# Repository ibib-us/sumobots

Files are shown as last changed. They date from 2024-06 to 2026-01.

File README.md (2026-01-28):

# IBiB Sumobots

It Begins in Brockport (IBiB) is developing its own sumobot league to introduce the community to competitive robotics.

Sumobots are robots that compete to push one another out of a ring. Ours are autonomous, which means they need to figure out how to do this all on their own. Ours are also built using inexpensive and easy-to-acuire materials, which means you can try out autonomous competitive robotics without having to invest a lot of cash.

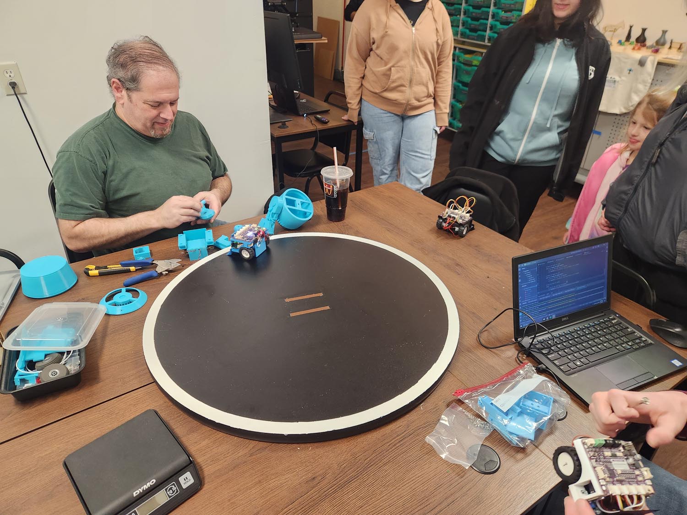
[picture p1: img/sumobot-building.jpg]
Sumo Louis


Here, you will find the hardware, the software and the rules for sumobots.

# Hardware

To be written. The files you need to 3D print the body of your sumobot are in the [stl](/stl/) directory.

# Software

The software can be found in the [code](/code/) directory. There are four files that are needed for your sumobot to run:

- `base_bot.py` contains the startup, searching, turning, and charging routines, along with some utility functions
- `code.py` is the main program that includes the fight sequence and the routine to start fighting
- `settings.py` contains parameters you can change to customize the fighting style of your sumobot
- `adafruit_vl5310x.mpy` is a special library to allow the time of flight (distance) sensor to operate properly

# Downloading the correct driver for the distance sensor

The sensor library you download depends on the version of CircuitPython you are running. The version can be found by looking at the `boot_out.txt` file on your sumobot. It will look something like this:

>Adafruit CircuitPython 7.1.0 on 2021-12-28; Cytron Maker Pi RP2040 with rp2040
>Board ID:cytron_maker_pi_rp2040

Since this sumobot is running version 7, it requires the version 7 library. However, Adafruit no longer supports this version, and it is recommended we upgrade to the latest (which is 9 at the moment - this is the version you can find in this repository). Here are the steps:

- Head to CircuitPython.org and download the `.UF2` file for the microcontroller. The direct link is [here](https://circuitpython.org/board/cytron_maker_pi_rp2040/).
- Find the `RST` button on your MakerPi2040 and double click it. You will now see that the CIRCUITPY drive on your computer disappears and is replaced by RPI-RP2.
- Copy the `.UF2` file that you downloaded onto this drive. Once completed, the RPI-RP2 drive will disappear
- Head over to the [Libraries](https://circuitpython.org/libraries) section and download the appropriate bundle, which is currently version 9.

## Initial setup
Open `settings.py` and review the "Robot hardware settings" section. Change any pin values if your hardware is connected differently than the default settings.

## Installation instructions
Make a backup copy of the code.py file that cam on your MakerPi board.
Copy the files `base-bot.py`, `code.py`, `adafruit_vl53l0x.mpy`, and `settings.py` to your MakerPi to get a working sumo bot.

## How to use
Turn on your MakerPi. To start a bout hold down the GP20 button until the light turns yellow. Your bot is now armed. Release the button to start the bout after a 5 second delay.
See the rules document for more detail on how Sumo bot matches operate.
Turn on your Maker Pi and press buttons until you find the one that turns the lights from red to yellow. Your bot is now armed. Release the button to enter FIGHT MODE!

## How to customize
Change values in the "Settings that control fight mode parameters" section of `settings.py` to make adjustments to your robot's fighting strategy.

## Advanced customization
Modify the `fight()` method in code.py to change your robot's fighting strategy.

## File descriptions 
* `settings.py` contains hardware pin assignments and basic behavior settings
* `code.py` defines the `fight()` method which determines the robot's logic while in fight mode.
* `base_bot.py` contains the main class which defines the fundamental methods for robot control such as moving and detecting enemies.
* `adafruit_Vl530x.mpy` is the driver for the time of flight sensors. The robot code won't work without it installed on the MakerPi.
* `original_code.py` is the default demo program that shipped with the MakerPI RP2040. It's not needed for the robot to work.

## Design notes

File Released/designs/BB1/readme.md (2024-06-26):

This is the complete plans for a mini sumo robot that conforms to IBiB2040 rules and is based around the Maker Pi RP2040 robotics board. It also comples with the generally used mini sumo rules.

An illustrated complete parts list is included in the "parts preparation.pdf" document.

Stl files for 3D printing the four body parts are included.

Illustrated assembly instructions can be found in the "assembly instructions.pdf" file.

Some notes on testing and changing the robot can be found in the "testing and tweaking.pdf" file.

The Maker Pi board should be running CircuitPython (it ships this way) and will need the code files in the code folder copied to it.

All material in this archive except the adafruit_vl53l0x.py file is CC0 "no rights reserved." adafruit_vl53l0x.py has a MIT license.  
Send any questions to: bill@tinkerfam.net

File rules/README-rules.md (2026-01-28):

# Rules README

*Note:* These rules are based on the gen 1 design (10 cm x 10 cm). They will be updated shortly.

- [rules for building your bot](./rules-robot.md)
- [rules for competing in a sumobot match](./rules-arena.md)

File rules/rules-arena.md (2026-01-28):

# IBiB Sumobot Arena Rules

**Event Summary:** Two robots compete in a head-to-head match following the basic system of traditional human sumo wrestling. Robots are autonomous. The objective is for a robot to push its opponent outside of the arena (doyho).

## I. Event Structure

### A. Arena

1. Competition area
    1. The name of the competition area is *dohyo*.
    2. The ring shall be circular in shape and 76 cm-77 cm (30 inches) in diameter. 
    3. The surface will be painted black or be blackbplastic with a 1 cm white line for a border. 
    4. The ring area extends to the outside edge of this circular line. 
    5. The dohyo will be at least 2.5cm in thickness.
2. Shikiri lines (starting lines) 
    1. Two painted parallel brown (or equivalent for absorption of IR light) lines centered in the ring
    2. The dimension of the shikiri lines are 1 cm in width, 10cm in length.
    3. The shikiri lines are spaced 10cm apart. 
    4. The separation distance between the lines is measured to their outside edges.
3. Dohyo exterior
    1. The area surrounding the dohyo is the *Shuhen*.
    2. There should be an appropriate space for recovering robots outside the outer edge of the ring. 
        1. This space can be of any color, and can be of any material or shape as long as the basic concepts of these rules are not violated. 
    2. This area, with the ring in the middle, is to be called the *arena*. 

**comments** The exact material for the dohyo is not specified. It may not be necessary to specify a material, only a set of characteristics such that the edge detection sensors can be adjusted to trigger only on the border and not on the shikiri lines and that the surface is suitable for the standard 2040b class blade and wheels. Should we add a diagram of the dohyo? Should we have a minimum distance for the shuhen?

### B. Format

1. The event is a double-elimination tournament. 
    1. Seeding is done randomly based upon the number of contestants entering the competition. 
    2. In the event that the bracket incorporates byes, they will be filled randomly.
2. Each robot competes in matches consisting of up to three bouts.
3. The winner of a match is the robot that wins two out of three bouts.
4. The winner of each match moves on in the winners bracket.
5. The loser of each match, if it is their first loss, moves to the losers bracket.
6. Ties are addressed in the section `C. Bout`
7. A robot is eliminated from the event after its second loss.
8. The judge overseeing the event is the gyoji.

### C. Bout 

1. A bout lasts a maximum of three minutes.
2. Contestant Positioning
    1. Contestants stand by the dohyo behind their respective shikiri lines.
3. Robot placement
    1. At the gyoji's command of "Position bots," contestants must immediately hold their robots directly over the area they intend to place them, approximately 15cm (6 inches) above the dohyo.
    2. The gyoji will then give the command "Place Bots," at which point contestants must lower their robots straight down onto the dohyo in one continuous motion, ensuring the final orientation is set during this movement.
    3. No additional adjustments to the robot's position or orientation are allowed after it has been placed on the dohyo.
    4. Failing to comply with these placement rules may be considered a minor violation. 
4. Starting the bout
    1. The robots must conform to the startup sequence described in `II.A. startup sequence`
    1. The gyoji instructs the contestants to arm their robots.
    2. With a countdown ("three, two, one, release"), the contestants initiate the start sequence of their robots and step away from the dohyo.
        1. Contestants should step away at least 30 inches from the edge of the dohyo.
5. False Start
    1. The gyoji may declare a false start if a robot starts before the word "release".
    2. The gyoji will declare a false start if they hear an audible sound from one of the robots prior to saying the word "release".
    3. After a false start, the offending robot is issued a penalty (shido).
    4. A robot receiving two shidos loses the bout.
6. Scoring and stopping the bout
    1. Earning points (Yuhkoh):
        1. A Yuhkoh is earned when a robot successfully pushes its competitor outside of the dohyo.
        2. A Yuhkoh is also earned if the competitor's robot exits the dohyo on its own.
        3. A Yuhkoh is awarded to a robot if its competitor receives two shidos.
    2. The Gyoji may stop a bout under several conditions
        1. A player is injured or about to be injured.
        2. The robots display no forward progress in the bout for 10 seconds.
        3. A robot is about to damage the dohyo.
        4. A robot has violated one of the rules.        
    3. Should a bout end with no contestant leaving the dohyo, gyoji will decide a winner and award a yuhkoh based upon technical merits in movement and operation of the robot, penalties accrued during the bout, and contestant attitudes during the bout.

**Comments** Should we provide examples of the decision making process in the event of a tie? It is possible that the gyoji cannot differentiate between the two sounds the robots are making, and therefore makes it difficult to determine who commits a false start. 

## II. Additional robot regulations

### A. Startup sequence
1. A startup sequence must be initiated by the press of button GP20
    1. Pressing and holding the GP20 button is referred to as "arming the robot".
    2. Releasing the GP20 button will continue the startup sequence.
2. The startup sequence must emit an audible tone to indicate the sequence has started
3. The startup sequence must blink the neopixel LEDs at 1 second intervals
4. The startup sequence must last for at least 5 seconds.
5. The wheel motors must be off during the startup sequence.

### B. Robot upgrades during competition
1. Contestants are not allowed to modify their robots after completing the class verification procedure unless specificly mentioned in these rules.
2. Sensor calibration (e.g. adjusting the potentiometers of edge detectors) 
    1. Utilizing the dohyo for sensor calibration is allowed prior to the start of the competition. 
    2. Contestants my not calibrate any sensors during their match.
    3. Contestants may perform sensor calibration without the use of the dohyo at other times during the competition.
3. Power (e.g. checking and replacing batteries)
    1. Batteries cannot be replaced after robots have completed their calss verification procedure.
    2. Under special circumstances, gyoji or the event manager may permit battery replacements, which will require class reverification. 

**Comments** Should we indicate the frequency and duration of the startup tone? Are there other startup sequence standardizations that should be implemented? Note that the mass difference between the super cheap zinc oxide and standard alkaline batteries is significant, so battery swap outs could result in a verified bot exceeding the weight limit.

## III. Violations and penalties

### A. Violations

1. Major violations
    1. A player who utters insulting words or puts voice devices in a robot to utter insulting words, or writes insulting words on teh body of a robot, is in violation of these rules.
2. Minor violations
    1. Entering the arena during the round without legitimate reason.
    2. Demanding to stop a match without appropriate reason.
    3. Taking more than 30 seconds before resuming a bout unless gyoji has announced a time extension.

### B. Penalties

1. In the event of a major violation, the contestant receives a kinjite (disqualification). All robots entered under the contestant are removed from the event.
2. In the event of minor violoation, the offending robot recieves a shido. Two shidos within one bout results in a Yuhkoh for the opponent.

## IV. Miscellaneous

### A. Declaring objections
1. No objections shall be declared against gyoji's decisions

### B. Safety Protocols
1. *reserved*

### C. Code of Conduct
1. *reserved*

### D. Technical Support
1. *reserved*

## V. Definitions

Bout
: A single 3-minute competition between two robots

Event
: A series of matches organized into a double-elimination bracket

Gyoji
: The referee/judge of a match.

Kinjite
: Disqualification from an event due to a major violation of the rules.

Match
: A series of up to three bouts

Shido
: A minor penalty. Two shidos within a bout results in a Yuhkoh for the opponent.

Yuhkoh
: A point, indicating that a bout has been won.

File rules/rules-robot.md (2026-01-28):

# IBiB Sumobot Design Rules

## I. General Specification

### A. Robot Classes

1. 2040b
    1. Must fit within a 10 cm by 10 cm square tube, with no height restriction.
    2. Maximum weight: 500 grams.
    3. Powered by no more than 6 volts.
    4. Must use the Maker Pi RP2040 development board as the microcontroller.
    5. Only the VL53L0X time of flight sensor and TCRT5000 reflectance sensor are allowed.
    6. Only two N20 metal gear DC motors are allowed.
    7. Must be programmed using CircuitPython.
2. 2040b+
    1. The 2040b+ class follows all the rules of the 2040b class except where specifically noted.
    2. No restrictions on the type and number of sensors.
    3. No restriction on the type and number of motors.

## B. Autonomy

1. All robots must be autonomous.
2. Any method of onboard control may be used, as long as it is fully contained within the robot and receives no external signals or directions (human, machine, or otherwise).
3. Autonomous robot operation must begin within the start procedure indicated for the event and robot class.

## C. Identification

1. Robots must have a name or number for registration purposes.
2. Robots must be clearly identifyable by their name and/or number.

## II. Restrictions

### A. Prohibited Devices and Materials

1. Jamming devices, such as IR LEDs intended to saturate the opponent's IR sensors, are not allowed.
2. Parts that could break or damage the event area are not allowed.
3. Parts intended to damage the opponent’s robot or its operator are not allowed. 
4. Parts intended to damage or alter the event area are not allowed.
5. Devices that can store liquid, powder, gas, or other substances for throwing at the opponent are not allowed.
6. Flaming devices are not allowed.
7. Devices that throw things are not allowed.
8. Sticky substances to improve traction are not allowed.
    1. Tires and other components of the robot in contact with the event area must not be able to pick up and hold a standard 3"x5" index card for more than two seconds.
    2. Devices to increase downforce, such as a vacuum pump or magnets, are not allowed.
9. All edges, including but not limited to the front scoop, must not be sharp enough to scratch or damage the ring, other robots, or players. Edges with a radius greater than 0.005", as would be obtained with an unsharpened 0.010" thick metal strip, should be acceptable. Judges or competition officials may require edges deemed too sharp to be covered with tape.

### B. Exceptions to restrictions

1. Restrictions mentioned in this section may be superceded by the event rules.
2. The judge or referee overseeing an event has final say on the interpretation of these restrictions.

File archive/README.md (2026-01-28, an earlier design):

# Archive

The archive contains older builds and design ideas for sumobots. They remain for historical value but we do not recommend they be used in current sumobot designs.

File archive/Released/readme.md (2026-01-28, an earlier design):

These files are released for public use as a starting point for builds of the IBIB2040 class of Mini Sumo Bots.
A rules document for competition is included.  
An example build is provided in the designs/BB1 folder. This includes a parts list and preparation document, an assembly document, and 3D printable files to create a chassis. A limited number of kits from this build are available.  
Software to be downloaded to the Maker PI2040 board can be found in the code folder.  
General information about the project can be found at https://ibib.us/projects/mini-sumo-robots/  
Send all inquries to Bill at bill@tinkerfarm.net.  

two

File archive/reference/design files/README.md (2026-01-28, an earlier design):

# sumobots
Schematics and datasheets for building and programming IBiB mini sumo bots
Contact Bill Ball, bill@tinkerfarm.net with any questions.

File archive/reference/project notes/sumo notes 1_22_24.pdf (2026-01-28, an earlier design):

IBiB Mini Sumo project notes. 1/21/2024. Bill Ball

The bots will meet standard specifications: 10cm x 10cm x unlimited, 500 grams max.

The bots will have the following components:

1. 4xaa battery holder. $0.5-$1. Is the 1x4 or 2x2 layout better? Builders supply their own batteries.

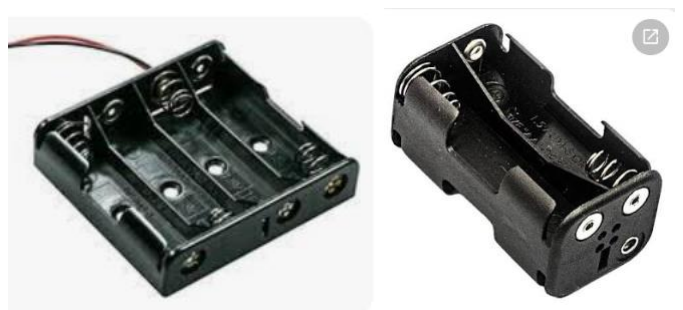
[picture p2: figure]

2. Maker Pi RP2040 main board with OEM Circuitpython 7 and accompanying 4 x grove to header pin wire sets. Cheapest source in bulk @$10: Newark. Manufacturer reference: https://www.cytron.io/p-maker-pi-rp2040-simplifying-robotics-with-raspberry-pi-rp2040 (https://www.cytron.io/p-maker-pi-rp2040-simplifying-robotics-with-raspberry-pi-rp2040)

The adafruit_vl5310x.mpy library will be installed by us. The default code.py will be renamed and a basic sumo bot program will be added as code.py.

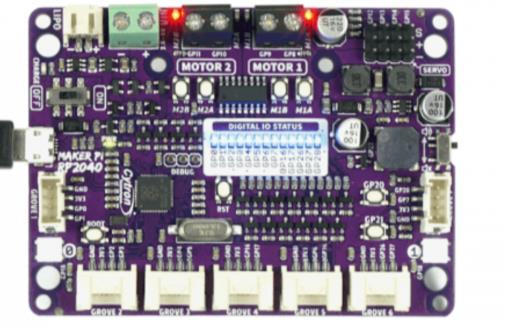
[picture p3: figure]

3. N20 6V motors (2). What rpm/torque trade off is best? We will start at 150rpm. $4.20 per pair from Aliexpress. We will need to solder on leads. Mounting brackets will be 3D printed (standard ones are too short for the wheels).

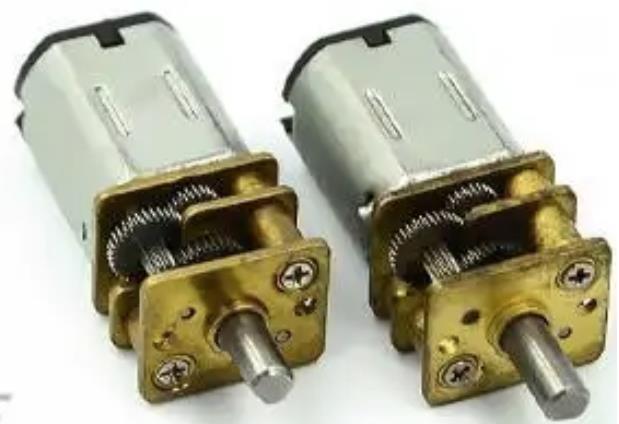
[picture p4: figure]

### 4. K346 43*19*3mm D-hole Rubber Wheel (2). $1.5 per pair from Aliexpress

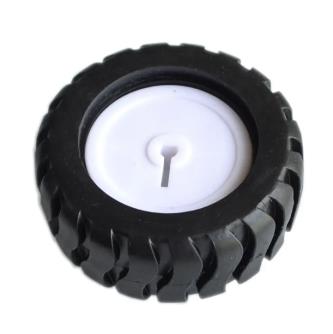
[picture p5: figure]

5. VL53L0X Time-of-Flight Ranging Sensor (2). $2.60 per pair from Aliexpress. We will need solder the header pins. We will use the VCC, GND, SCL, SDA, and XSHUT pins. XSHUT is required to change the I2C address in software. We are not planning to use the GPI01 (data ready) pin (it would require an additional grove wire set if we do). If two sensors doesn’t work well we may need to go to three, which would require 2 additional grove wire sets and may not all fit on the same I2C bus as exposed by the Maker pi.

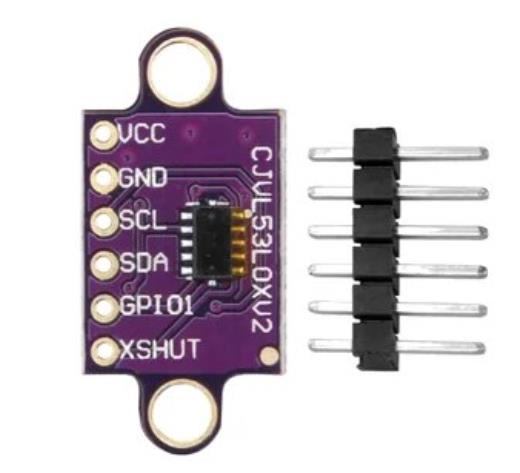
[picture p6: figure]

6. TCRT5000 Infrared Reflective Sensor Module (2). $1.5 per pair from Aliexpress.

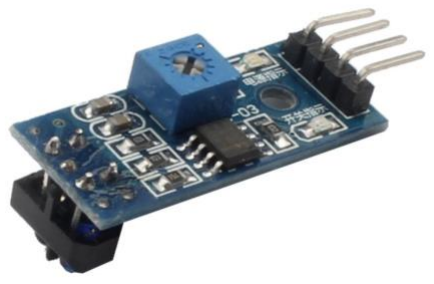
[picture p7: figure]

7. USB A to micro USB cable for programing. We may want to offer other formats to micro options. $1 from Aliexpress. People don’t otherwise acquire micro USB cables anymore.
8. Chassis. etc. The chassis can be user designed/built. We will need to develop a design for 3D printing, maybe laser cut or even milled. We also need to decide on ballast and fasteners. The basic bot only weighs about 250 grams. We should supply enough repositionable ballast to reach 500 grams. I use steel BBs but they need to be contained. We can do this project with m2 Philips head fasteners throughout. It would be incredibly kind to builders if fasteners are all the same length. 14mm? As a supplied kit let’s plan on $5 total cost of supplies.

Total delivered cost is currently about $27 for supplies when items are purchase qty 10 or greater using mostly Aliexpress.

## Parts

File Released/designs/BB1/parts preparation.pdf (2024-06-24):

Parts preparation information for the Mini Sumo BB1 robot.

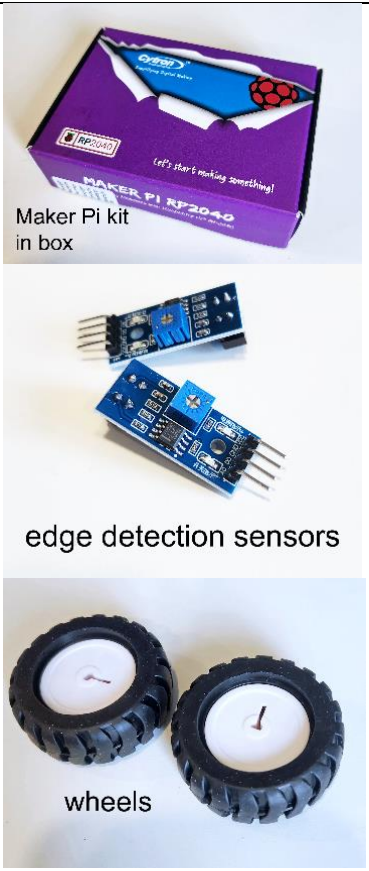
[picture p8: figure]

1. The parts list for the robot (included in kits
except where noted):

A Maker Pi RP2040 kit in box. The box includes one Maker Pi board, 4 Grove connector to female header pin cables, a mini screwdriver, and 4 adhesive feet. The feet are not used in this project.

Two ToF (VL53L0X Time of Flight) sensors of the type pictured in this document. The header pints are pre-soldered on the sensors included in the kit.

Two edge detection (TCRT5000 infrared reflective) sensors of the type pictured in this document (with right angle header pins, sensor and adjustment screw on opposite sides).

Two N20 6 volt gear head motors, low torque models only. 150 or 200 rpm motors suggested.

Wire and heat shrink for motor leads if they are not pre-soldered to the motors. The leads are pre-soldered in kits.

Two 43mm x 19mm treaded tires mounted on 3mm D shaft wheels, as shown.

One 4 x AA battery holder of the type pictured in this document, along with 4 AA batteries.

A minimum of ten m3 x 10mm pan head screws (referred to as bolts in the documentation).

One m3 x 10mm countersunk screw (referred to as bolts in the documentation).

A minimum of 11 nuts for the m3 bolts.

Four 3D printed body parts.

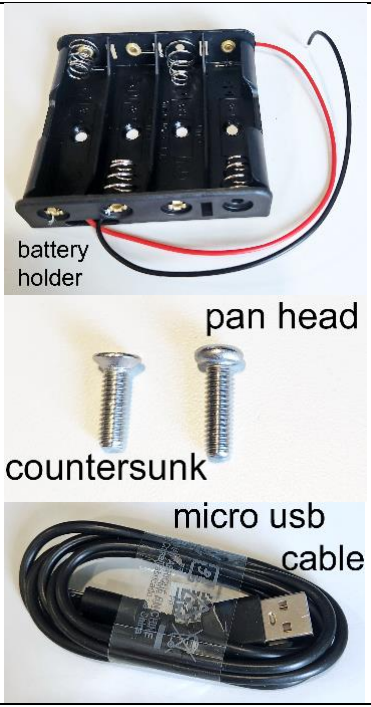
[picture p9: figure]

Ballast weight as desired. About 200 grams of steel BBs are suggested and included in kits. These need to be kept from getting loose. They can be left in the bag when inserted in the main compartment of the robot body or mixed with a small amount of glue (not included in kits) to distribute them among multiple compartments in the body. ALL parts of the robot should be weighed to make sure it is below 500 grams before the BBs are glued into place.

A micro USB cable for programming, along with downloaded software.

A Phillips screwdriver. There is one in the Maker Pi box but it is smaller than ideal.

Small needle-nosed pliers. These are not included in the kit.

Access to a scale to weigh the finished robot and make sure it does not exceed 500 grams. Not included in the kit.

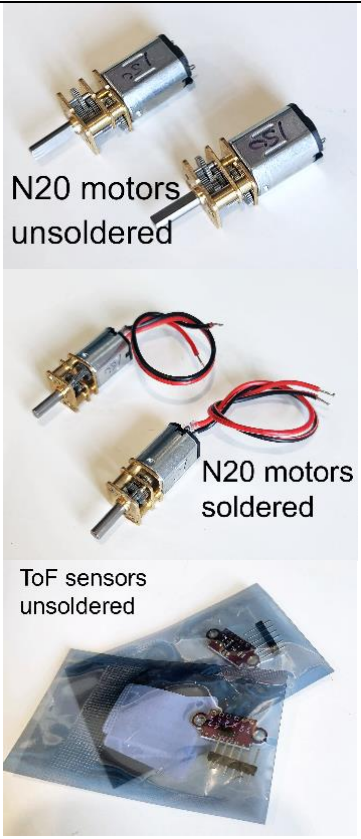
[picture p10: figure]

2. If the motor wires are not soldered to the motors and this exposed wire at the connection covered with heat shrink, this will need to be done with two pairs of wire, about 80mm long.

The edge detection sensors usually ship with right angle header pins already soldered on and in anti-static bags. They do not need further preparation.

The ToF sensors usually ship unsoldered with header pins included in the anti-static bag.

The yellow protective film covering the black rectangle on the ToF sensors will need to be removed if it has not already been done. It has been removed from sensors in kits.

If the ToF sensors have not had their header pins soldered on, this will need to be done. The longer pins are in the back of the sensor and it is soldered from the front.

3. The four 3D printed parts of the BB1 robot body: main body, fender bar, lid, and blade can be printed with standard settings. Printing time varies widely but plan on 8 hours of print time total. Kits include parts usually printed in PLA, which is brittle so be careful to not force it while constructing the robot. PETG is a more forgiving material if you are printing your own parts.

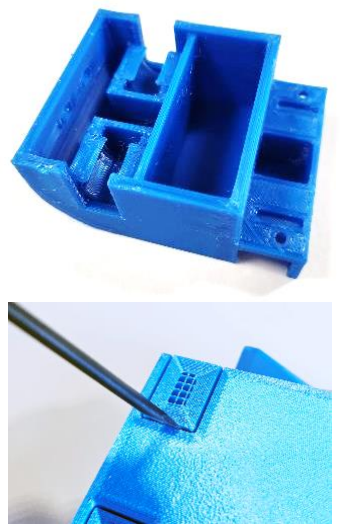
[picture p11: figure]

Only the main body needs to be printed with supports. The body is printed upright on the printer bed, as shown. Once it is off the printer the supports can be removed by popping them off the side of the body and at the curved rear from underneath. The supports interface to the main body does not need to be cleaned up fully, although the bolt holes should be cleared.

The fender bar is printed “face” down on the bed, as shown.

The lid should be printed upside down on the bed, as shown, with the flat side on the bed.

The blade is printed with its back (the flattest part) on the bed, as shown. It does not need supports.

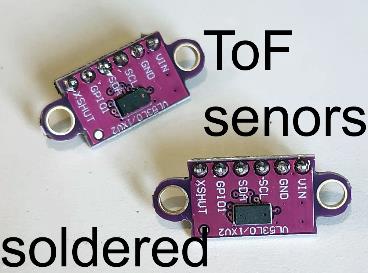
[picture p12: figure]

# Main Body

# Fender Bar

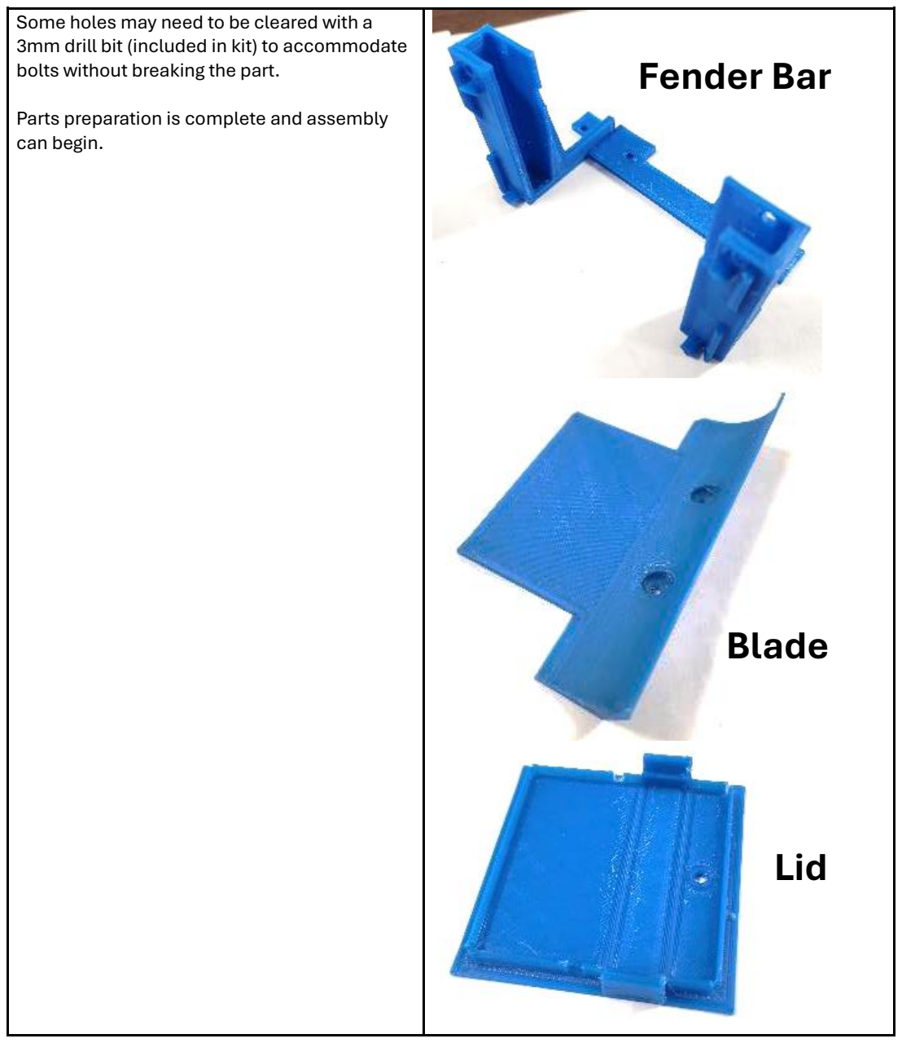
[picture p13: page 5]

Some holes may need to be cleared with a 3mm drill bit (included in kit) to accommodate bolts without breaking the part.

Parts preparation is complete and assembly can begin.

# Blade

# Lid

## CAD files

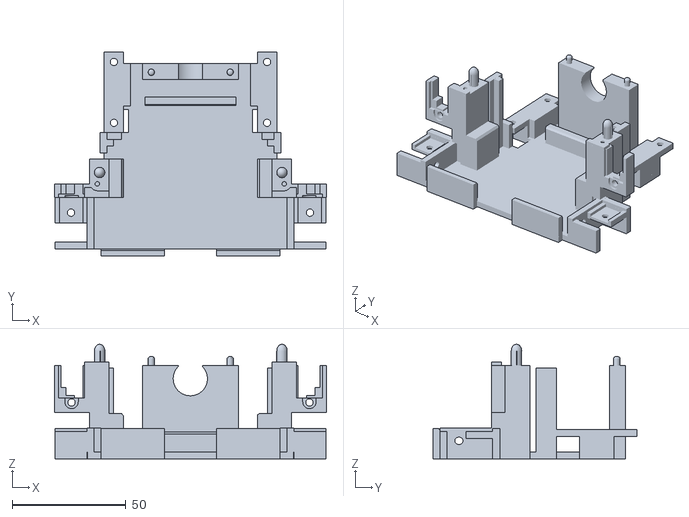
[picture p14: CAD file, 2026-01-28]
stl/ks4 chassis.stl
119.3 x 89.4 x 50.3

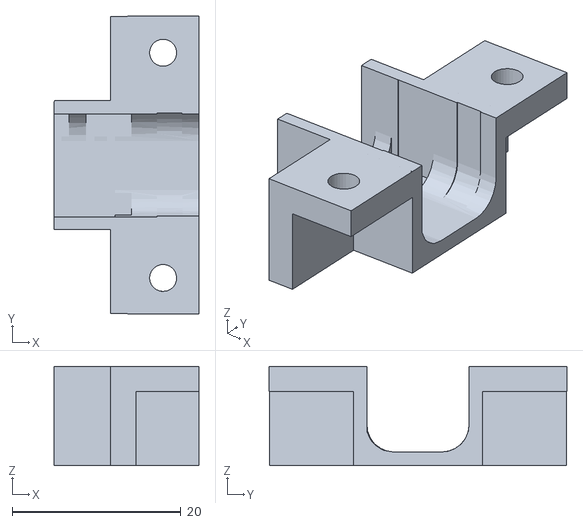
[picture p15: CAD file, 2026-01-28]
stl/ks4 mount.stl
17.2 x 35.3 x 11.8

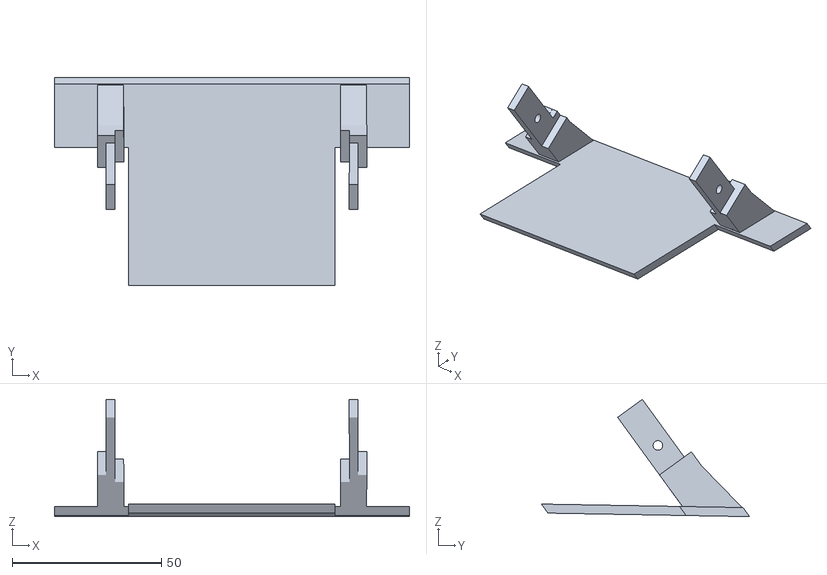
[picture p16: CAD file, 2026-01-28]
stl/ks4 blade1.stl
119.0 x 69.8 x 39.3

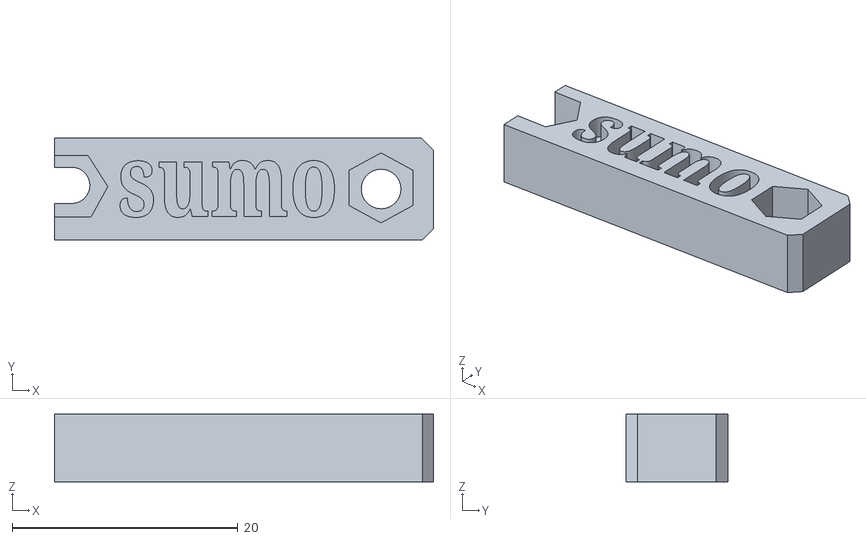
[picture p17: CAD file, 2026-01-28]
stl/ks4 wrench.stl
33.6 x 9.00 x 6.00

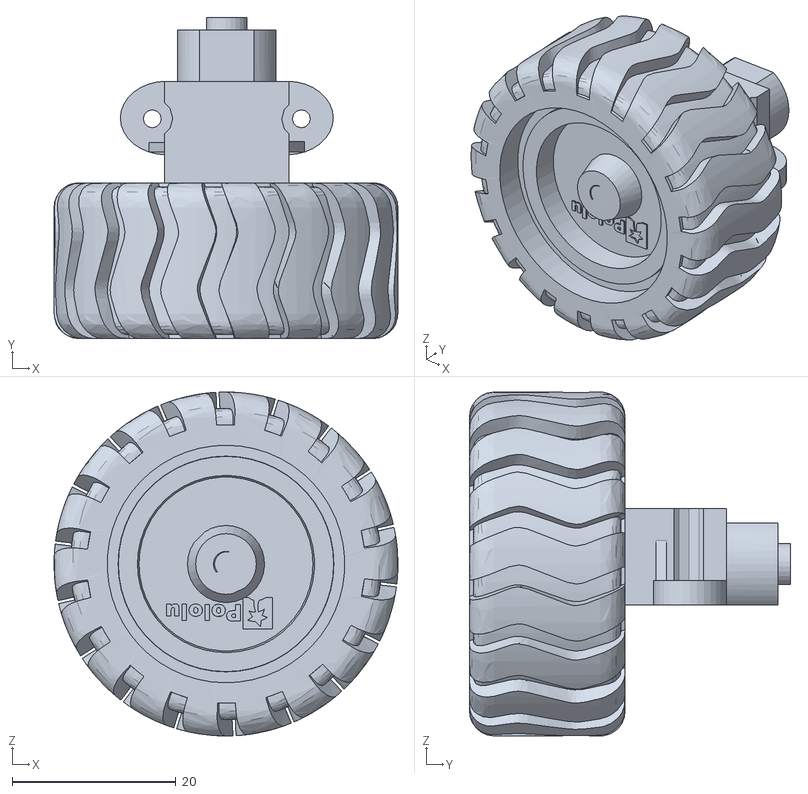
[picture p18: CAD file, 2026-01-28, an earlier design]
archive/reference/design files/3D CAD files/wheelmotormount assembly.stl
42.0 x 39.2 x 42.0

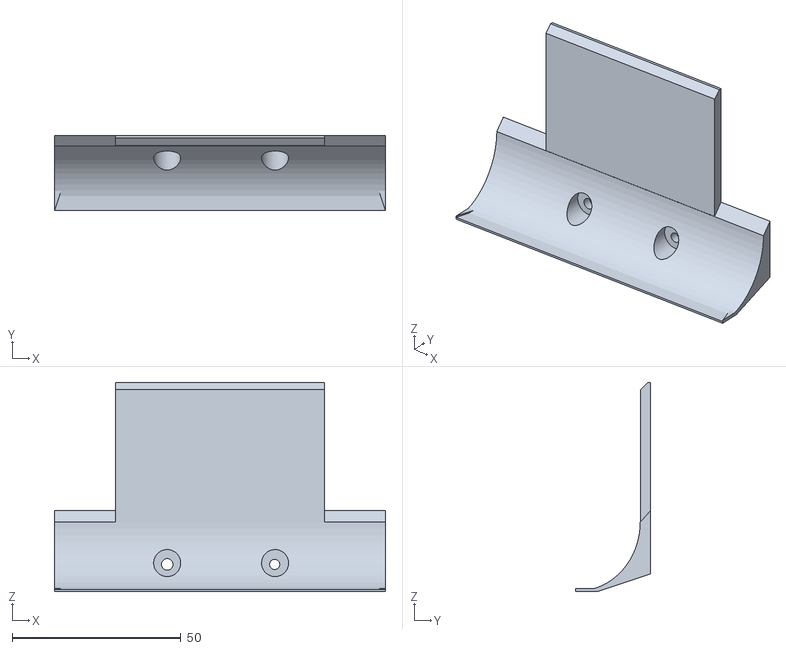
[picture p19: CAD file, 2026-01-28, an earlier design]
archive/Builders/Bill Ball/BB1/Sumo BB1 blade.stl
98.0 x 22.2 x 62.0

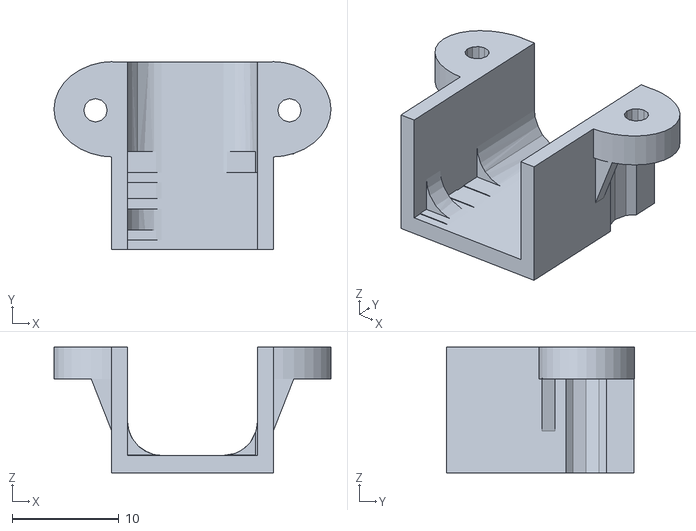
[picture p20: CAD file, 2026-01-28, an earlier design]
archive/reference/design files/3D CAD files/n20_motor_mount.stl
26.0 x 17.6 x 11.8

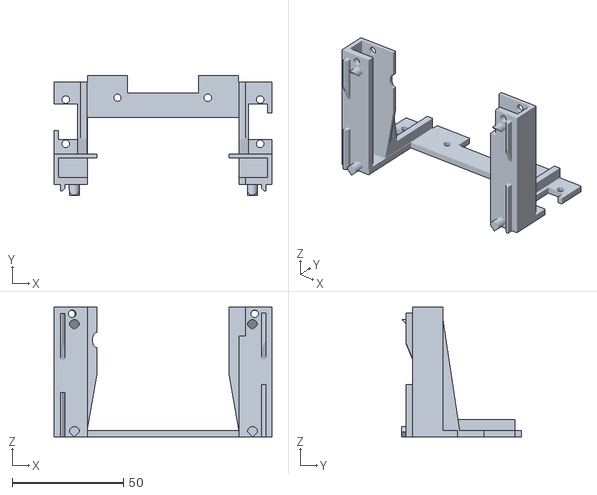
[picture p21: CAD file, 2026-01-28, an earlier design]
archive/Released/designs/BB1/Sumo BB1 fender bar.stl
97.9 x 53.9 x 58.4

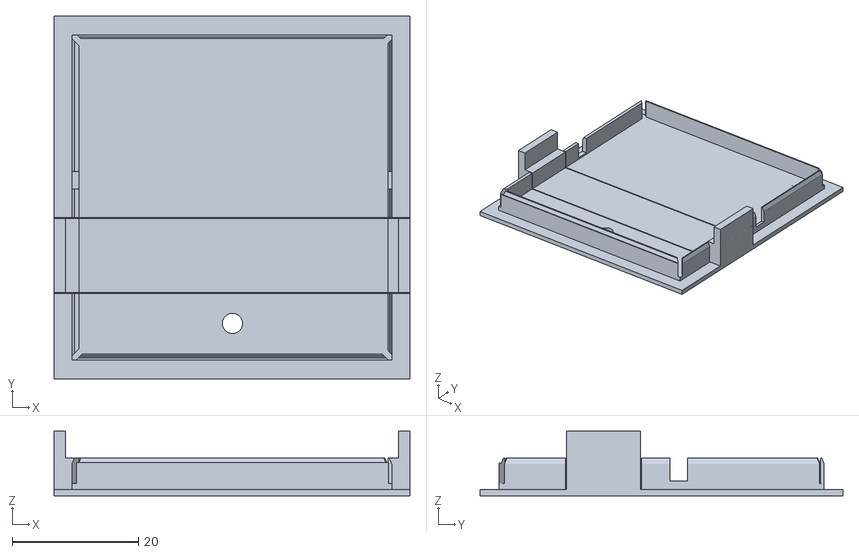
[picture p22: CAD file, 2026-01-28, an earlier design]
archive/Builders/Bill Ball/BB1/Sumo BB1 lid.stl
56.5 x 57.6 x 10.3

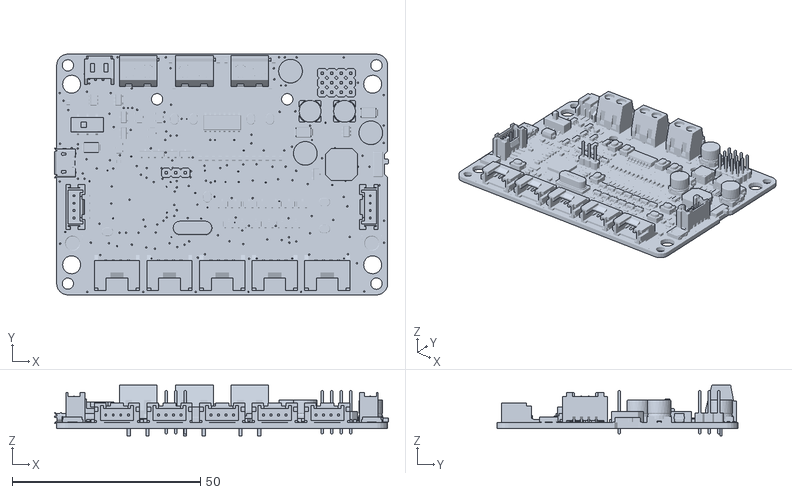
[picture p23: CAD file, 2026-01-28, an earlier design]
archive/reference/design files/3D CAD files/MAKER-PI-RP2040 lowres.stl
88.8 x 64.0 x 13.5

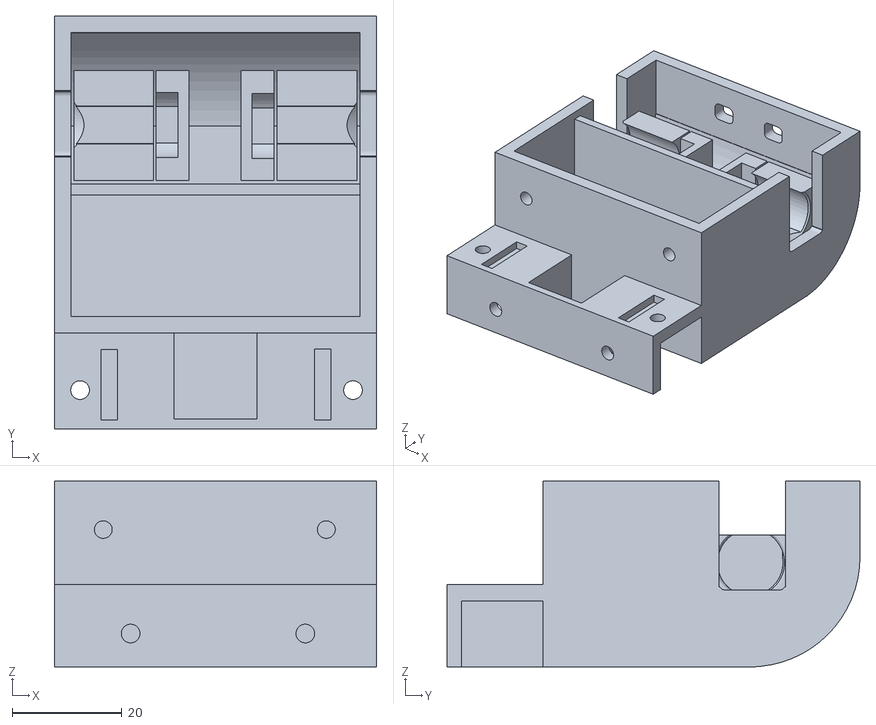
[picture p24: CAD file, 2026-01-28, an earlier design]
archive/Builders/Bill Ball/BB1/Sumo BB1 body.stl
58.6 x 75.2 x 33.8

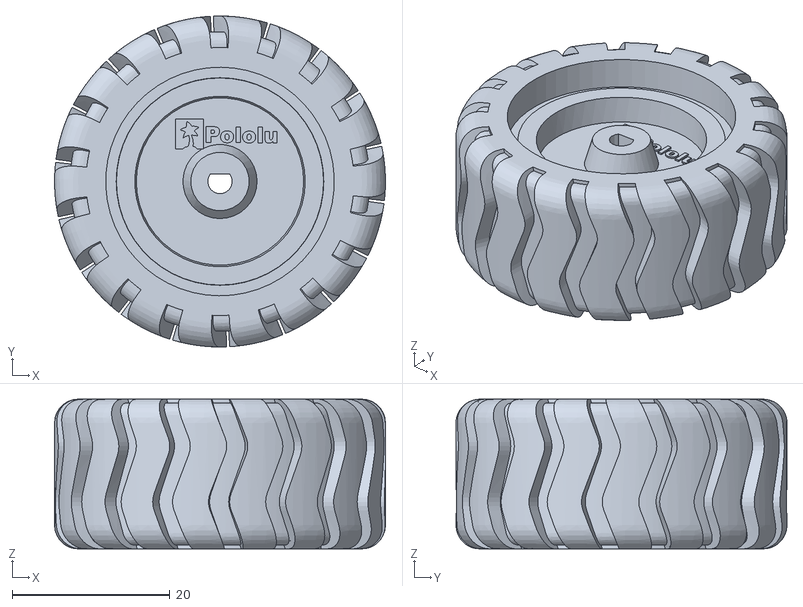
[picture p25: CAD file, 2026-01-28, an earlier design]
archive/reference/design files/3D CAD files/K345-wheel-42x19mm lowres.stl
42.0 x 42.0 x 19.0

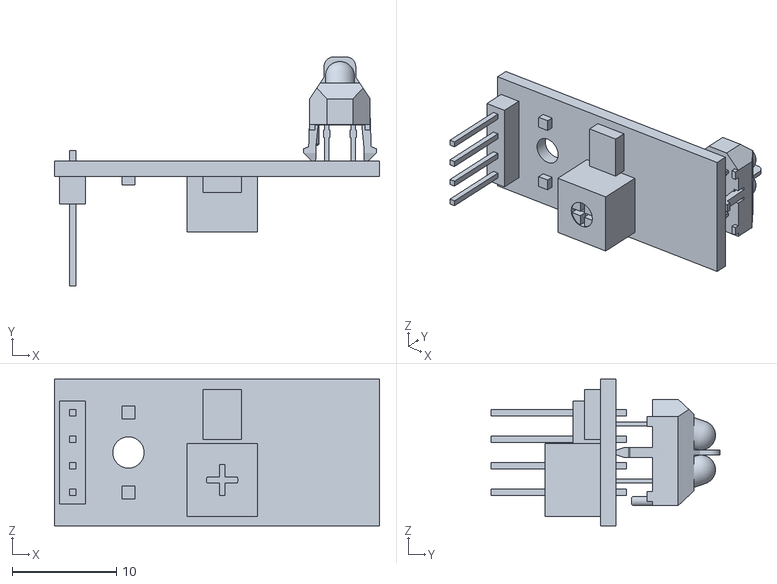
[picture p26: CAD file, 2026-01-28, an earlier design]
archive/reference/design files/3D CAD files/TCRT5000 sensor.stl
31.2 x 22.0 x 14.1

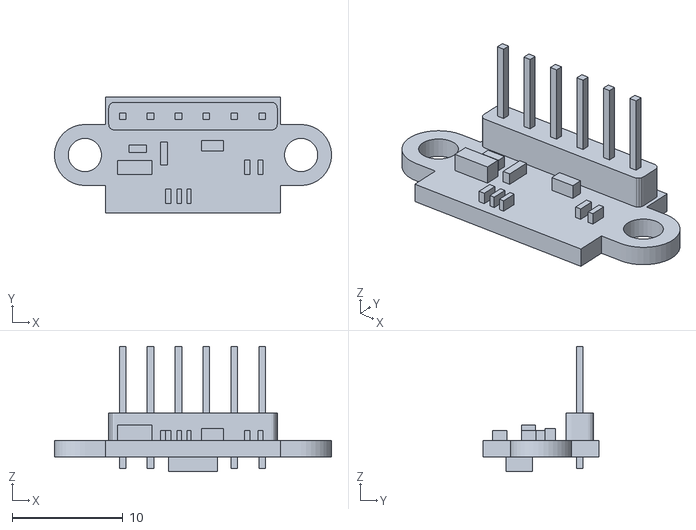
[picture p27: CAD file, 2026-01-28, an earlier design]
archive/reference/design files/3D CAD files/VL53L0X TOF Sensor.stl
25.0 x 10.5 x 11.3

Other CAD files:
archive/reference/design files/3D CAD files/1x4 AA battery holder.stl
archive/reference/design files/3D CAD files/2x2 AA battery holder.stl
archive/reference/design files/3D CAD files/K346-wheel-42x19mm.f3d
archive/reference/design files/3D CAD files/MAKER-PI-RP2040.f3d
archive/reference/design files/3D CAD files/N20_gear_motor.stl

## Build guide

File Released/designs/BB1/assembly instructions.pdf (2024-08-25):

Assembly instructions for BB1 mini sumo bot. Please consult the parts preparation information before assembly.

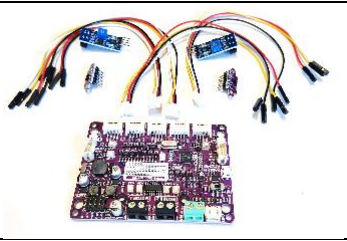
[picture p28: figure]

1. Lay out the electronics for the robot. This
includes the Maker Pi RP2040 board (qty. 1) with grove connecter cables (qty. 4), ToF (VL53L0X Time of Flight) sensors (qty. 2), and Edge Detection (TCRT5000 infrared reflective) sensors (qty. 2).

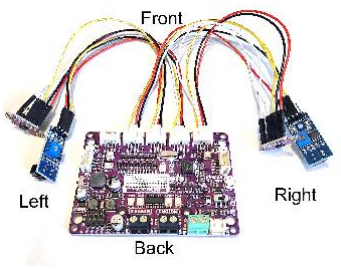
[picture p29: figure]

2. Connect the electronics according to the following list, using the labels on the parts. The Grove port numbers and pins are listed on both the top and the bottom of the Maker Pi board. All sensors have connection labels on them. Note that all references to “left,” “right,” etc. in these instructions refer to the robot’s point of view.

Grove 2
GND – BLK -> Right ToF GND 3V3 – RED -> Right ToF VIN GP2 – WHT -> Right ToF SDA
GP3 – YEL -> Right ToF SCL

Grove 3
GND - BLK -> Left Edge Detection GND 3V3 - RED -> Left Edge Detection VCC GP4 - WHT -> Left ToF XSHUT (Note: This wire does not go to the left Edge Detection sensor with the others on this connector) GP5 - YEL -> Left Edge Detection DO

Grove 4
GND - BLK -> Left ToF GND
3V3 - RED -> Left ToF VIN
GP16 - WHT -> Left ToF SDA GP17 - YEL -> Left ToF SCL

Grove 5
GND - BLK -> Right Edge Detection GND 3V3 - RED -> Right Edge Detection VCC GP6 - WHT -> Right ToF XSHUT (Note: This wire does not go to the right Edge Detection sensor with the others on this connector) GP26 - YEL -> Right Edge Detection DO

Set the electronics assembly aside while keeping track of the left/right orientation of parts. It’s a good idea to mark L or R on the sensors with a sharpie.

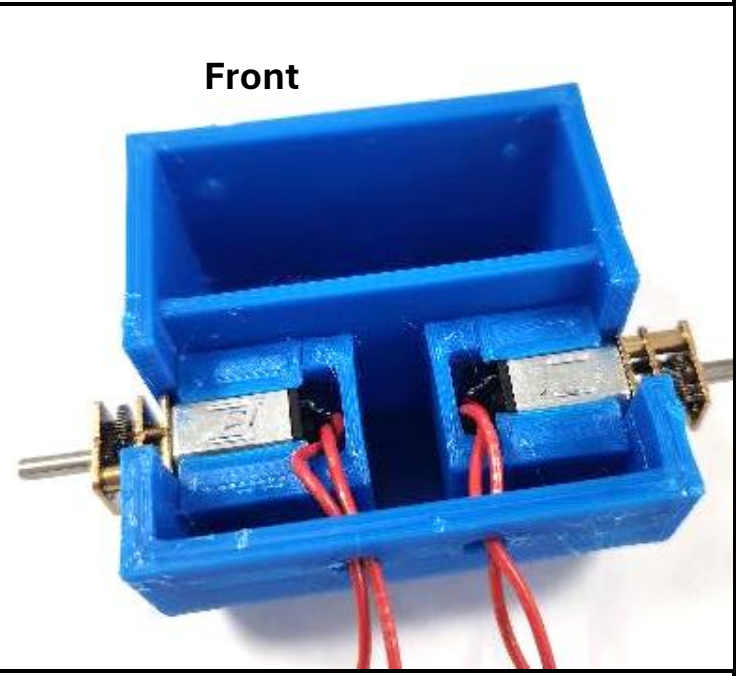
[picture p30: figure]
Front

3. Insert the motors into the main body. It doesn’t matter which motor goes into which side.

Carefully, pre-bend the wire close to the motor end cap if needed. The motors are held in the robot by friction, and it may require some pressure to insert them fully. Hold them by the brass plates on their gearbox while inserting. Ideally the brass plate closest to the silver motor housing should align with the inside of the main body wall, as illustrated. However, as long as it aligns with the outside of the wall installation will be adequate. Forcing the installation could crack the main body. Thread the motor wires up and out of the main body through the supplied holes at the back of the body.
4. Install the fender bar onto the main body with two bolts inserted from the front and secured with nuts from inside the front wall of the main body.

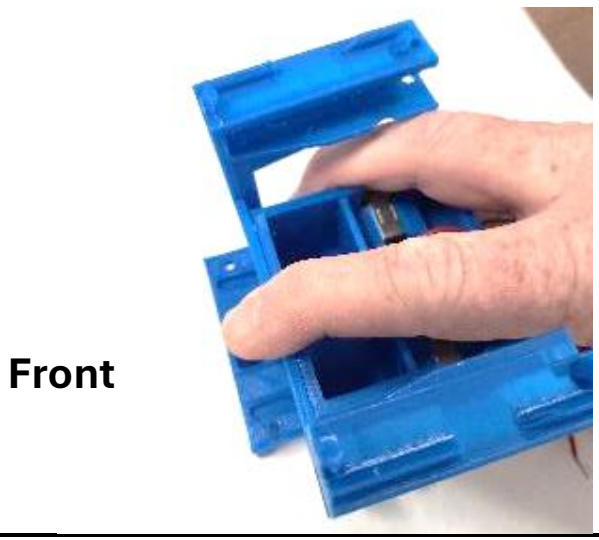
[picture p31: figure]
Front

Note that the fender bar is easily bent in some directions and applying pressure in those directions can warp or even break it. Do not squeeze or twist the bar or put pressure on it from the top. Instead, always hold it flat against the main body while installing and put any pressure on the main body.

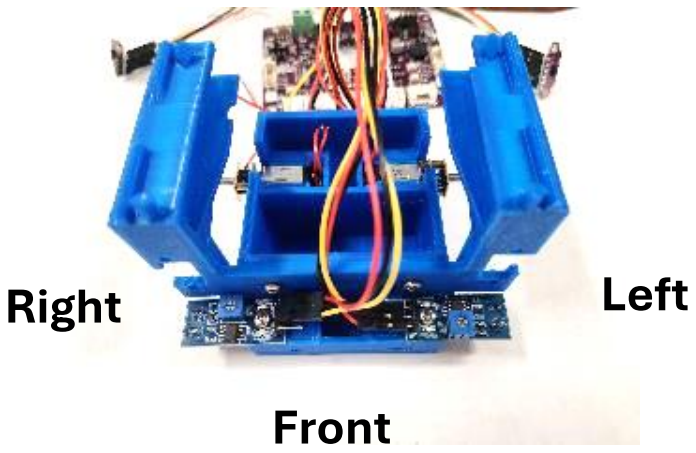
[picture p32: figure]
Right; Left; Front

5. If the front ballast box is being used, fill the box and secure the ballast. BBs will get loose and roll all over. If these are used they should be mixed with some sort of glue and poured in (not illustrated). Allow the glue to set before proceeding.

Install the edge detectors to the main body by bolting them down from the top and securing them underneath with nuts. Bolt the left sensor (attached to Grove port 3) to the left side of the robot and the right sensor to the right side. The blue adjustment screw blocks on the sensors point upward, and one block sits closer to the main body than the other. You can alternate (interlace) the wires from the left and right sensors so they fit better in the space available. The sensors need to snug up against the fender bar so they do not hang over the edge where the blade attaches.

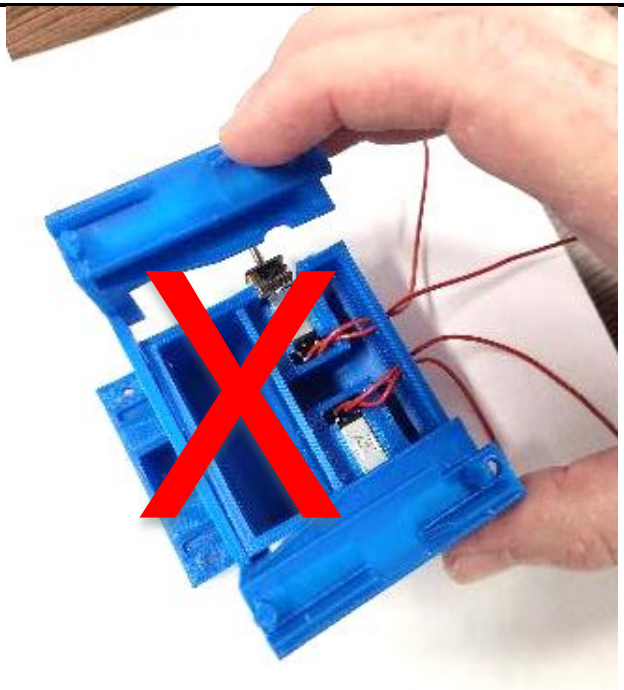
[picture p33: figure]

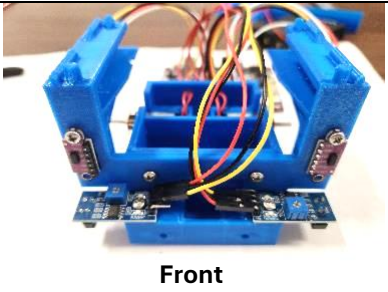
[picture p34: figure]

6. Insert and mount the ToF sensors. Insert the correct sensor into the correct side of the body. The left sensor is attached to Grove port 4 for VIN and GND. Secure the sensors with a bolt at the top of each sensor and a nut inside the top hole on the fender bar. The bottom of the sensor does not need a bolt (the bottom holes are there to be used in case the top ones break out). Note that the black rectangles on the sensors are at the outside edges of the robot. | Front

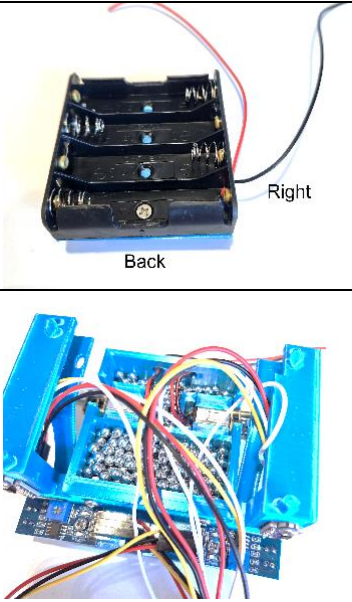
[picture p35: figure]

7. Mount the battery box to the flat side of the lid using the countersunk bolt. Bolt from the inside of the battery box through the box and lid and secure underneath with a nut. The top of the bolt should not be above the top of the inside of the battery holder bottom so that the batteries will install fully. The battery wires should be on the right side of the assembly with the bolt in the rear hole in the box, as shown.
8. If the main body will be ballasted, fill one or both compartments with ballast. If the ballast is electronically conductive is important that the ballast cannot come into contact with the soldered tabs at the back of the motors. Here steel BBs are being used (on an older chassis design), but they are too large to come into contact with the motor tabs.

Round ballast will easily roll out of the ballast box and spill widely so it can be kept in a plastic bag when putting it in the ballast box or glued into place. It is important to weigh all your robot’s components together to make sure your robot will not exceed 500 grams.

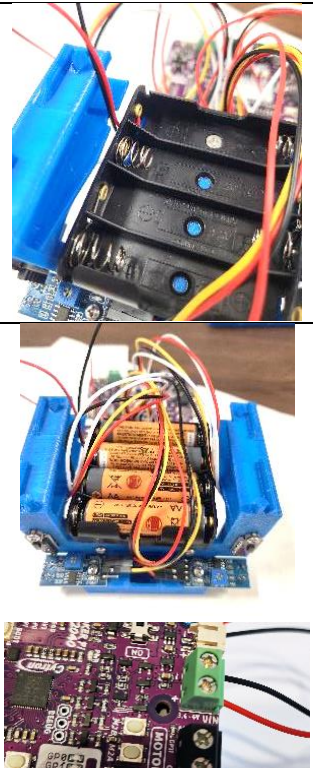
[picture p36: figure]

9. Add the lid/battery box assembly to the main body. It should snap into place on all four sides. There is a notch in the fender bar that will allow the battery wires to come up into it.
10. Install the batteries in the orientation shown on the battery box. Read below First.

Be aware that the battery wires are now live (there is no on/off switch on the battery box) and the exposed ends can give a shocking lesson in how many watts 4 AA batteries can produce. Do not let the exposed ends of the battery wires contact each other or short against anything conductive, particularly the Maker Pi board. It is a good idea screw them down to the green terminal block on the Maker Pi board prior to installing the batteries. The screws on the block open to provide a clamp to secure the wires when closed. Make sure the black battery wire is secured to the clamp marked “-” on the front of the block and the red wire to the clamp marked “+” to have the correct polarity. The exposed wire (but not the insulated part) should be fully enclosed by the terminal block clamps. If not, set the On/Off Maker Pi power switch to the Off position.

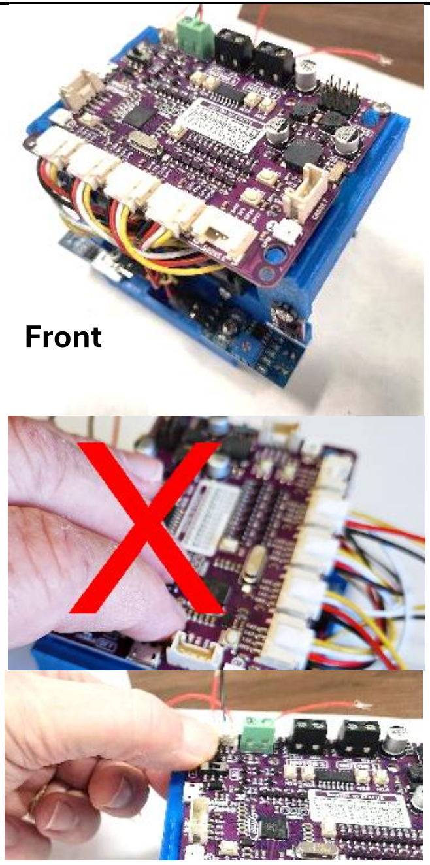
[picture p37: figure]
Front

11. The extra wiring can be rolled into loops and placed between the top of the battery holder and the top of the fender bar. Loose wire should not be left where the wheels will go.

The Maker Pi board can be snapped into place over the posts in the fender bar. The white grove connectors go at the front.

Do not attempt to snap the Pi board down by pressing down from above. This will permanently warp or possibly break the fender bar.

Instead, snap the front of the board into the posts at the front of the robot by squeezing the board and the top layer of the fender together on both sides. It may be difficult the first time it is done. Then snap the board to the rear posts on both sides by squeezing the board and the top layer of the fender together at the back, as shown.

The board can be bolted down to the fender bar using the holes at the back.

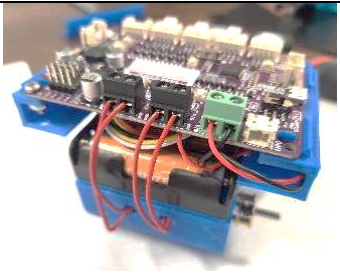
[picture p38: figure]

12. Screw the exposed ends of the motor wires to the black “Motor 1” terminal (for the left motor) and the “Motor 2” terminal (for the right motor) on the battery board. At this point it doesn’t matter which wire goes to which clamp on the terminal as motors do not have polarity and these wires can easily be reversed if you find your robot goes backwards when you want it to go forward.

Tuck in the wiring by pushing the battery wires into the right fender channel and pushing the motor wires into the main body. The extra length will be needed later to change batteries without unscrewing the wires.

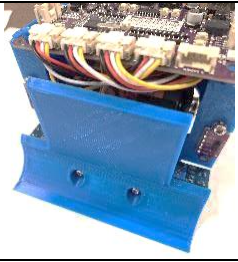
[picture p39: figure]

13. Attach the front blade to its mount on the main body by inserting two bolts from the front for the blade and securing them with nuts underneath. The front of the blade will be slightly lower than the main body. The robot will sit level once the wheels are attached.

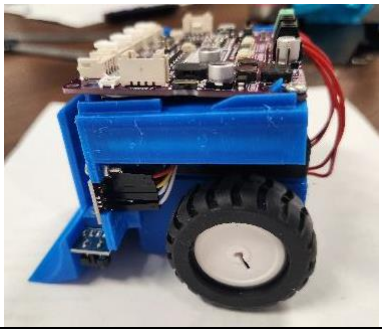
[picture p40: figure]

14. Mount the wheels and tires with the flatter side of the wheel to the outside. The motor shafts have a D shape and this should be aligned the D shape on the wheel before they are pressed on. They should be against the main body without being so tight against it that they cause friction.

Note how the wires from the ToF sensors are pulled up into the fender bar so they don’t rub on the wheels.

Assembly is complete. Now is a good time to make sure your robot will fit with the regulation width of 10 cm and length of 10 cm (loosely fitted wheels and wires may cause it to be oversized).

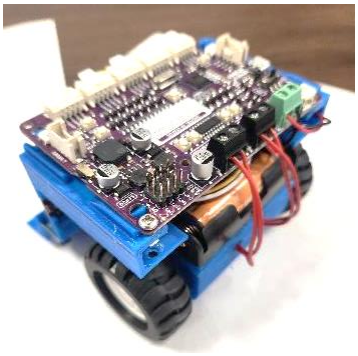
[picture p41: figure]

15. If software has not been downloaded it can be done now. Connect your robot to a computer using the USB cable. Using Thonny, Mu or other Python editor download 5 files to your robot from our repository: Adafruit_vl5310x.mpy, base_bot.py, code.py, settings.py, and original_code.py.

The Maker Pi board must be turned on to download software or run the robot. The power switch on the Maker Pi board is marked with ON and OFF settings.

When it is time to change the batteries, you can do so without tools. Pull the extra wire from batteries and the motors out from storage and spread them apart enough to clear the battery box. Gently lift the lid/battery box off the main body and slide it out of the back of the robot to replace the batteries.

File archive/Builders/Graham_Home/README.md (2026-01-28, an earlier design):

## How to use this code:
1. Copy the folder "adafruit bus device" and the file "adafruit_vl53l0x.mpy" from the [Adafruit CircuitPython Bundle](https://circuitpython.org/libraries) to the "lib" folder on your MakerPi.
2. Copy all .py files from the code/ directory to your MakerPi.
3. MakerPi NeoPixels will light up red. Hold the GP20 button and release it (NeoPixels will turn yellow when button is held and green when button is released).
4. You are now in sumo mode! Robot will seek out an opponent and attempt to shove it out of the ring. 

You can run `copy-code.ps1` on a Windows computer to copy the code files to your MakerPi, just remember to update 
the `copy-code.ps1` script with the correct path to the code directory and the correct drive letter for the MakerPi.

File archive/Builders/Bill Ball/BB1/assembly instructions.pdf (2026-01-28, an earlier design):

Assembly instructions for BB1 mini sumo bot. Please consult the parts preparation information before assembly.


1. Lay out the electronics for the robot. This
includes the Maker Pi RP2040 board (qty. 1) with grove connecter cables (qty. 4), ToF (VL53L0X Time of Flight) sensors (qty. 2), and edge detection (TCRT5000 infrared reflective) sensors (qty. 2).


2. Connect the electronics according to the following list, using the labels on the parts. The Grove port numbers and pins are listed on both the top and the bottom of the Maker Pi board. All sensors have connection labels on them. Note that all references to “le ft,” “right,” etc. in these instructions refer to the robot’s point of view.

Grove 2
GND -> Right ToF GND
3V3 -> Right ToF VIN
GP2 -> Right ToF SDA
GP3 -> Right ToF SCL

Grove 3
GND -> Left edge detection GND 3V3 -> Left edge detection VIN GP4 -> Left ToF XSHUT
GP5 -> Left edge detection DO

Grove 4
GND -> Left ToF GND
3V3 -> Left ToF VCC
GP16 -> Left ToF SDA
GP17 -> Left ToF SCL

Grove 5
GND -> Right edge detection GND 3V3 -> Right edge detection VCC GP6 -> Right ToF XSHUT

GP26 -> Right edge detection DO

Set the electronics assembly aside while keeping track of the left/right orientation of parts. It’s a good idea to mark L or R on the sensors with a sharpie.

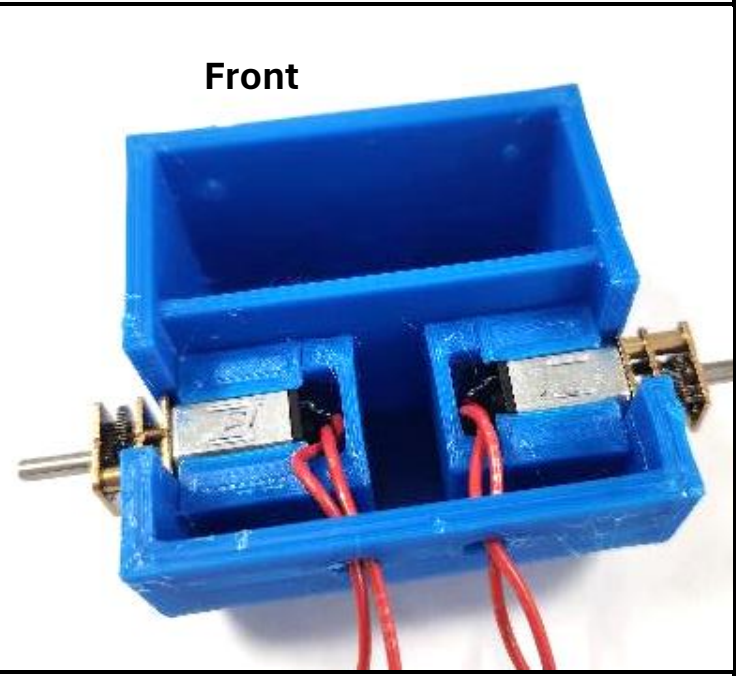
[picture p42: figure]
Front

3. Insert the motors into the main body. It doesn’t matter which motor goes into which side.

The motors are held in the robot by friction, and it may require some pressure to insert them fully. Hold them by the brass plates on their gearbox while inserting. Ideally the brass plate closest to the silver motor housing should align with the inside of the main body wall, as illustrated. However, as long as it aligns with the outside of the wall installation will be adequate. Forcing the installation could crack the main body. Thread the motor wires up and out of the main body through the supplied holes at the back of the body.

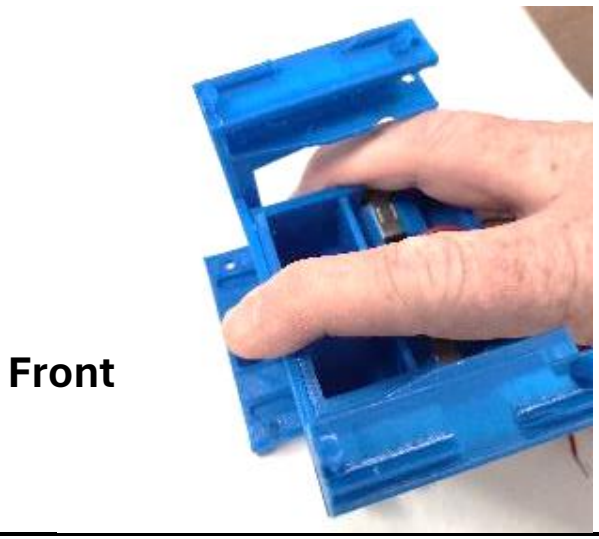
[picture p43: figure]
Front

4. Install the fender bar onto the main body with two bolts inserted from the front and secured with nuts from inside the front wall of the main body.

Note that the fender bar is easily bent in some directions and applying pressure in those directions can warp or even break it. Do not squeeze or twist the bar or put pressure on it from the top. Instead always hold it flat against the main body while installing and put any pressure on the main body.

5. If the front ballast box is being used, fill the box and secure the ballast. BBs will get loose and roll all over. These should be mixed with some sort of glue and poured in if used (not illustrated). Allow the glue to set before proceeding.

Install the edge detectors to the main body by bolting them down from the top and securing them underneath with nuts. Bolt the left sensor (attached to Grove port 3) to the left side of the robot and the right sensor to the right side. The blue adjustment screw blocks on the sensors point upward, and one block sits closer to the main body than the other.

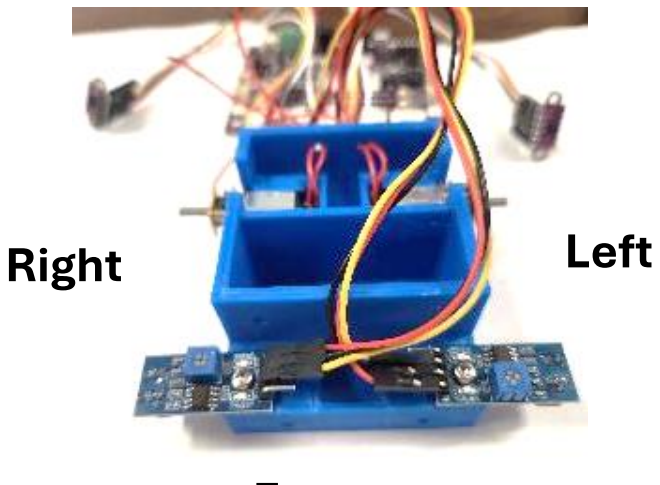
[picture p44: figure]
Right; Left

## Front

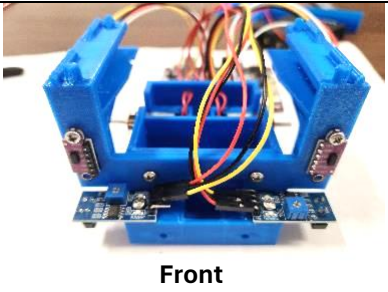
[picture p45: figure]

6. Insert and mount the ToF sensors. Insert the correct sensor into the correct side of the body. The left sensor is attached to Grove port 4 for VCC and GND. Secure the sensors with a bolt at the top of each sensor and a nut inside the top hole on the fender bar. The bottom of the sensor does not need a bolt (the bottom holes are there to be used in case the top ones break out). Note that the black rectangles on the sensors are at the outside edges of the robot. | Front


7. Mount the battery box to the flat side of the lid using the countersunk bolt. Bolt from the inside of the battery box through the box and lid and secure underneath with a nut. The top of the bolt should not be above the top of the inside of the battery holder bottom so that the batteries will install fully. The battery wires should be on the right side of the assembly with the bolt in the rear hole in the box, as shown.
8. If the main body will be ballasted, fill one or both compartments with ballast. If the ballast is electronically conductive is important that the ballast cannot come into contact with the soldered tabs at the back of the motors. Here steel BBs are being used (on an older chassis design), but they are too large to come into contact with the motor tabs.

Round ballast can easily roll out of the ballast box and spill widely until secured with glue and the glue has set. It’s important to weigh all of your robot’s components together before the glue has set to make sure your robot will not exceed 500 grams.

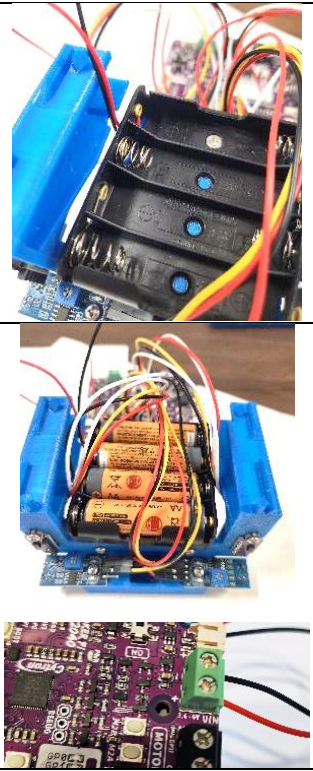
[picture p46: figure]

9. Add the lid/battery box assembly to the main body. It should snap into place on all four sides. There is a notch in the fender bar that will allow the battery wires to come up into it.
10. Install the batteries in the orientation shown on the battery box.

Be aware that the battery wires are now live (there is no on/off switch on the battery box) and the exposed ends can give a shocking lesson in how many watts 4 AA batteries can produce. Do not let the exposed ends of the battery wires contact each other or short against anything conductive. It’s a good idea screw them down to the green terminal block on the Maker Pi board right away. The screws on the block open to provide a clamp to secure the wires when closed. Make sure the black battery wire is secured to the clamp marked “-” on the front of the block and the red wire to the clamp marked “+” to have the correct polarity. The exposed wire (but not the insulated part) should be fully enclosed by the terminal block clamps.

Front

11. The extra wiring can be rolled into loops and placed between the top of the battery holder and the top of the fender bar. Loose wire should not be left where the wheels will go.

The Maker Pi board can be snapped into place over the posts in the fender bar. The white grove connectors go at the front.

Do not attempt to snap the Pi board down by pressing down from above. This will permanently warp or possibly break the fender bar.

Instead, snap the front of the board into the posts at the front of the robot by squeezing the board and the top layer of the fender together on both sides. It may be difficult the first time it is done. Then snap the board to the rear posts on both sides by squeezing the board and the top layer of the fender together at the back, as shown.

The board can be bolted down to the fender bar using the holes at the back.


12. Screw the exposed ends of the motor wires to the black “Motor 1” terminal (for the left motor) and the “Motor 2” terminal (for the right motor) on the battery board. At this point it doesn’t matter which wire goes to which clamp on the terminal as motors do not have polarity and these wires can easily be reversed if you find your robot goes backwards when you want it to go forward.

Tuck in the wiring by pushing the battery wires into the right fender channel and pushing the motor wires into the main body. The extra length will be needed later to change batteries without unscrewing the wires.


13. Attach the front blade to its mount on the main body by inserting two bolts from the front for the blade and securing them with nuts underneath. The front of the blade will be slightly lower than the main body. The robot will sit level once the wheels are attached.


14. Mount the wheels and tires with the flatter side of the wheel to the outside. The motor shafts have a D shape and this should be aligned the D shape on the wheel before they are pressed on. They should be against the main body without being so tight against it that they cause friction.

Note how the wires from the ToF sensors are pulled up into the fender bar so they don’t rub on the wheels.

Assembly is complete. Now is a good time to make sure your robot will fit with the regulation width of 10 cm and length of 10 cm (loosely fitted wheels and wires may cause it to be oversized).

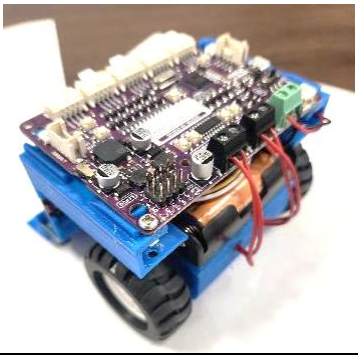
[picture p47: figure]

15. If software has not been downloaded it can be done now.

The Maker Pi board has to be turned on to download software or run the robot.

When it is time to change the batteries you can do so without tools. Pull the extra wire from batteries and the motors out from storage and spread them apart enough to clear the battery box. Gently lift the battery off the main body and slide it out of the back of the robot to replace the batteries.

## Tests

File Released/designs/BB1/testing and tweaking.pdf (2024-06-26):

Testing and tweaking notes for the BB1 mini sumo robot.
Testing
After you have completely assembled your robot and downloaded the needed files to it (Adafruit_vl5310x.mpy, base_bot.py, code.py, settings.py, and original_code.py) you are ready to do some testing and basic calibration.
Moving the power switch on the Maker Pi board to on should light up a small green LED next to PWR on the board, showing that the board has power. It should also light two larger LEDs (0 and 1) in red showing that the code.py program is running. If you don’t have power check the battery connections and the correct insertion of the batteries into the holder. If you get the power LED but don’t get the red LEDs the correct software has not been downloaded. The small blue LEDs on the Maker Pi board indicate the presence of the sensors, but not if they have been connected entirely correctly. With power turned on, blue LEDs should be lit for GP2, GP3, GP4, GP6, GP16, and GP17.
To test movement, it is best to use a black surface with a white border. Probably the easiest thing to use is a black poster board with a white paper border of at least 2.5cm wide taped around it.
Place your bot on the black surface and turn it on. You should see a single green LED lit on each edge sensor. Move the bot to a white surface. You should see two green LEDs lit on each edge sensor. If you don’t get the second green LED when the bot is on white you should adjust the small white dial on the edge sensor with a screwdriver until the second LED lights up.
A dummy opponent such as a block of wood or weighted box about the same size as the robot can be added to the black test surface. Clear an area of at least 60cm from the edges of your test surface.
With the robot on the black surface and powered up, press and hold the GP20 button on the Maker Pi board. The large LEDs should turn yellow-green, indicating the robot is ready to battle. When the GP20 button is released the LEDs should turn green and the robot should beep. If the robot doesn't beep, it is possible the mute switch on the Maker Pi board has been toggled to off.
The LEDs will flash as the robot counts 5 seconds. Make sure you and everything else is clear of your test area by at least 60cm at this time to avoid false targets.

After a 5 second pause the robot should start searching for an opponent. It should find your dummy opponent and attempt to push it out of the test area. When your robot reaches the white edge of the test area it should attempt to stop and turn back into the black area.
The robot should immediately charge forward if it faces a nearby opponent. If your robot moves in an unpredictable manner, such as backing up or spinning when you expect it to go forward, you most likely need to change the order the motor wires are connected to the terminals on the Maker Pi board. Use a screwdriver to switch one pair at time.
Tweaking and beyond
If you get this far you are ready to compete. However, you can fine tune the performance of your robot by changing values in the settings.py file. The default settings work ok but they are not optimized to win matches. You should experiment with your test set up and dummy opponent to find settings that you think are best.
You are also encouraged to decorate your robot and you will be required to have a name for it at events.
There are more advanced ways to customize your IBiB2040 min sumo robot:
You can design your own chassis for the sumo bot. An easy way to start is to copy and modify the reference BB1 design on Tinkercad at: https://www.tinkercad.com/things/64lSNJw5qik-mini-sumo-ibib2040-bb1
Parts to be 3D printed are light blue in that file, the manufactured parts are in gray.
If you are an experienced Python programmer you can edit the code.py and other files, although the start-up sequence has to be unchanged.
The rules for this class also allow some flexibility in component selection.
Read the complete rules document to guide you in customizing within what is allowed for the IBiB2040 class of mini sumo robots.

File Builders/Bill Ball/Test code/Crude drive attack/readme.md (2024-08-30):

This is a simple test program to see if the bot is working.
It should not be used for competition.

Send any questions to: bill@tinkerfam.net

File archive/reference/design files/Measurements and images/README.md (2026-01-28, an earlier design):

# sumobots
Measurements and images of components for IBiB mini sumo bot.
This is to accompany CAD files.
Note that some commodity parts (i.e. battery holders) may vary slightly in dimensions.
Contact Bill Ball, bill@tinkerfarm.net with any questions.

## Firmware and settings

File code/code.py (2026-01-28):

from settings import *
from sumobot import *
import time
import random

# Set offsets to zero, place a large object about 6-10 inches from the sumobot,
#  and confirm that the same distance is measured with both TOF sensors.
#  Adjust offsets as needed.
tof_left.offset = 0
tof_right.offset = -60

# Initialize the current conditions
conditions = get_conditions()

# Define FSM states
state = {
    "IDLE"      : 0, # Sitting around doing nothing - can be exited by hitting the start button (BUTTON 0)
    "WAITING"   : 1, # Waiting to start the battle - following the start routine, will exit to searching
    "SEARCHING" : 2, # Looking for an opponent
    "CHARGING"  : 3, # Moving towards what bot thinks is an opponent
    "RETREATING": 4, # Moving away from the opponent
    "AVOIDING"  : 5, # Found the edge of the doyho and is moving around.
    "TESTING"   : 6, # A special state for debugging
    "NOSTATE"   : 7, # A special state for the start of the bot. It will never be here.
}

# Make it easy to get the state name from its number
state_name = {v: k for k, v in state.items()}

# FSM variables
# Set current_state to "TESTING" and you can minuplate the testing state to provide debug information
# Otherwise, set it to "IDLE"
current_state = state["IDLE"]
previous_state = state["NOSTATE"] # This forces the logger to log the first entry into IDLE
last_state_change_time = 0
timer = [0] * len(state) # Give each state a timer for things like blinking lights, moving motors
microstate = None # Needed a global variable in some states (e.g. in what direction is an edge being avoided
testing = False # Set to true to enter the TESTING state instead of starting a match

# FSM update function
def update_fsm():
    '''
    The state machine is a bunch of conditional statements that follow the general template of an entrance conditional, update statements,
        and an exit conditional.
    '''
    global current_state, previous_state, microstate, last_state_change_time, conditions, testing

    if current_state == state["IDLE"]:
        '''
        What does this state do? It does nothing except wait for a button press to move on to the next state.
        '''
        # Variables useful for this state
        pixels_on = (0,255,0)
        pixels_off = (255,0,0)
        event = conditions['key_events'] # to simplify typing

        # Enter state
        if not current_state == previous_state:
            previous_state = current_state
            pixels.fill((255,0,0))
            move(STOP)
            log(f"Entered {state_name[current_state]} state.", LOG_INFO)

        # Update state
        if event and event.key_number == 0 and event.pressed:
            pixels.fill(pixels_on)
            if testing: # Will switch to TESTING
                log("Will switch to TESTING state when button is released.", LOG_INFO)
            else:
                pixels.fill((255,255,0))
        elif event and event.key_number == 0 and event.released:
            if testing:
                current_state = state["TESTING"]
            else:
                current_state = state["WAITING"]
            last_state_change_time = time.monotonic()
            log(f"Button released, will switch to {state_name[current_state]}", LOG_INFO)

        # Exit state
        if not current_state == previous_state:
            log(f"Left {state_name[current_state]} state.", LOG_INFO)
            pixels.fill((0,0,0))
# /// end of IDLE state ///

    elif current_state == state["WAITING"]:
        '''
        What does this state do? It performs the five second (with blinking lights) delay before the bot can start attacking.
        '''
        pixels_on = (0,255,0)
        pixels_off = (0,0,0)

        # Enter
        if not current_state == previous_state:
            previous_state = current_state
            pixels.fill(pixels_on)
            log(f"Entered {state_name[current_state]} state.", LOG_INFO)
            timer[current_state] = last_state_change_time # Start the light blinking timer
            buzz() # Make some noise.

        # Update
        if time.monotonic() - last_state_change_time >= WAITING_TIME:
            pixels.fill(pixels_off)
            current_state = state["SEARCHING"]
            last_state_change_time = time.monotonic()
        elif time.monotonic() - timer[current_state] > 0.5:
            # In this state, both pixels are the same color, so we only probe the first one.
            timer[current_state] = time.monotonic()
            log(f'Pixel status in WAITING {pixels}', LOG_DEBUG)
            if pixels[0] == pixels_on:
                pixels.fill(pixels_off)
            else:
                pixels.fill(pixels_on)

        # Exit state
        if not current_state == previous_state:
            log(f"Left {state_name[current_state]} state.", LOG_INFO)
            pixels.fill(pixels_off)
# /// end of WAITING state ///

    elif current_state == state["SEARCHING"]:
        '''
        What does this state do? It rotates the bot to the right until it senses an opponent, at which point
            it switches to the CHARGING state. It will pay attention to the edge and enter AVOIDING if necessary.
        '''
        pixels_on = (0,0,255)
        pixels_off = (0,0,0)

        # Enter
        if not current_state == previous_state:
            previous_state = current_state
            pixels.fill(pixels_on)
            log(f"Entered {state_name[current_state]} state.", LOG_INFO)
            timer[current_state] = last_state_change_time # What is timer used for?
            microstate = random.randint(0,1) # to make searching a bit variable this variable is shared, so it will be problematic

        # Update
        if conditions["edge_left"] or conditions["edge_right"]:
            log("Edge detected, switching to AVOIDING state.", LOG_INFO)
            current_state = state["AVOIDING"]
            dit(5)
            move(BACKWARD) # Don't want to wait until next update or else it may be too late
            last_state_change_time = time.monotonic()
        elif conditions["tof_left"] < MAX_DISTANCE or conditions["tof_right"] < MAX_DISTANCE:
            log("Opponent detected, switching to CHARGING state.", LOG_INFO)
            dit(3)
            move(FORWARD) # Waiting for next update and we may miss the opponent.
            current_state = state["CHARGING"]
            last_state_change_time = time.monotonic()
        else:
            # Perform search movements (arcing)
            if microstate == 1:
                move(HARD_RIGHT)  # Adjust as needed to implement the arc-search strategy
            else:
                move(HARD_LEFT)

        # Exit state
        if not current_state == previous_state:
            log(f"Left {state_name[previous_state]} state. Going to {state_name[current_state]} state.", LOG_INFO)
            pixels.fill(pixels_off)
# /// end of SEARCHING state ///

    elif current_state == state["CHARGING"]:
        '''
        What does this state do? It heads toward the opponent, adjusting left/right as needed. It will back off
            after a user-defined time and try to attack again.
        '''
        pixels_on = (255,0,255)
        pixels_off = (0,0,0)

        # Enter
        if not current_state == previous_state:
            previous_state = current_state
            pixels.fill(pixels_on)
            log(f"Entered {state_name[current_state]} state.", LOG_INFO)
            timer[current_state] = last_state_change_time # What is timer used for?

        # Code to update current state
        if conditions["edge_left"] or conditions["edge_right"]:
            log("Edge detected, transitioning to AVOIDING state.", LOG_INFO)
            current_state = state["AVOIDING"]
            move(BACKWARD) # Don't want to wait or might be too late.
            last_state_change_time = time.monotonic()
        if abs(conditions["tof_diff"]) > CHARGE_TOLERANCE: # Bot might be heading in the wrong direction
            log("Shifting approach", LOG_DEBUG)
            if conditions["tof_diff"] > 0: # Bot needs to turn right
                move(RIGHT)
            else:
                move(LEFT)
        else:
            move(FORWARD)
        if time.monotonic() - timer[current_state] > CHARGE_DURATION: # Give up on charging forward
            log("Stalemate detected, retreating", LOG_INFO)
            current_state = state["RETREATING"]
            last_state_change_time = time.monotonic()

        # Exit state
        if not current_state == previous_state:
            log(f"Left {state_name[current_state]} state.", LOG_INFO)
            pixels.fill(pixels_off)
# /// end of CHARGING state ///

    elif current_state == state["RETREATING"]:
        '''
        What does this state do? The bot backs up from where it thinks there is an opponent. It makes a hard left turn
            and then resumes searching. It will continue to monitor for the edge.
        '''
        pixels_on = (0,255,255)
        pixels_off = (0,0,0)

        # Enter
        if not current_state == previous_state:
            previous_state = current_state
            pixels.fill(pixels_on)
            log(f"Entered {state_name[current_state]} state.", LOG_INFO)
            timer[current_state] = last_state_change_time # What is timer used for?
            random_direction = random.randint(0,1)
            if random_direction == 1:
                move(BACK_LEFT)
            else:
                move(BACK_RIGHT)

        # Code to update current state
        if conditions["edge_left"] or conditions["edge_right"]:
            log("Edge detected, switching to AVOIDING state.", LOG_INFO)
            current_state = state["AVOIDING"]
            move(BACKWARD) # Don't want to drive too far off the doyho
            last_state_change_time = time.monotonic()
        if time.monotonic() - timer[current_state] > RETREAT_TIME/2:
            move(BACKWARD)
        if time.monotonic() - timer[current_state] >  RETREAT_TIME:
            log("Done with retreat", LOG_INFO)
            current_state = state["SEARCHING"]
            last_state_change_time = time.monotonic()

        # Exit state
        if not current_state == previous_state:
            log(f"Left {state_name[current_state]} state.", LOG_INFO)
            pixels.fill(pixels_off)
            move(STOP)
# /// end of RETREATING state ///

    elif current_state == state["AVOIDING"]:
        '''
        What does this state do? Back up and turn away from the edge of the doyho. The state implements a 'microstate'
            which tells the fsm if it is avoiding from one of the edges or both.
        '''
        pixels_on = (255,255,255)
        pixels_off = (0,0,0)

        # Enter
        if not current_state == previous_state:
            previous_state = current_state
            # Back up as soon as possible
            move(BACKWARD)
            pixels.fill(pixels_on)
            log(f"Entered {state_name[current_state]} state.", LOG_INFO)
            timer[current_state] = last_state_change_time # What is timer used for?
            if conditions["edge_left"]:
                if conditions["edge_right"]: # hit edge straight on, so back-up and turn
                    microstate = 0
                else:
                    microstate = 1
            elif conditions["edge_right"]: # Shouldn't need elif, but just in case.
                microstate = -1



        # Code to update current state
        # perform movement - breaking up total avoidance time into two phases, a backup and a hard turn.

        if time.monotonic() - timer[current_state] > AVOIDANCE_TIME/2: # The /3 may be worth making a parameter
            if microstate == -1:
                move(HARD_RIGHT)
            else:
                move(HARD_LEFT)
        if time.monotonic() - timer[current_state] > AVOIDANCE_TIME:
            log("Switching to SEARCHING state.", LOG_INFO)
            current_state = state["SEARCHING"]
            last_state_change_time = time.monotonic()

        # Exit state
        if not current_state == previous_state:
            log(f"Left {state_name[current_state]} state.", LOG_INFO)
            pixels.fill(pixels_off)
            # make sure we aren't moving
            move(STOP)
            # clear the microstate
            microstate = None
# /// end of AVOIDING state ///

    elif current_state == state["TESTING"]:
        '''
        What does this state do? Nothing useful. This state is used to test your code and could be used to prototype
            new states if desired.
        All logs are set to critical to make sure they are printed.
        Set move_test to True to check motors
        Set log_conditions to True to view the sensor readings
        '''

        log_conditions = True
        move_test = False
        # Some variables for this state
        pixels_on = (255,0,0)
        pixels_off = (0,0,0)

        # Enter
        if not current_state == previous_state:
            previous_state = current_state
            pixels.fill(pixels_on)
            log(f"Entered {state_name[current_state]} state.", LOG_CRITICAL)
            timer[current_state] = time.monotonic()
        # Update
        if log_conditions:
            log(get_conditions(), LOG_CRITICAL)
            log(round(float(battery.value/65536)*100),LOG_CRITICAL)

        if move_test:
            if time.monotonic() - timer[current_state] < TEST_TIME:
                move(FORWARD)
                log("Moving forward", LOG_CRITICAL)
            elif time.monotonic() - timer[current_state] < 2*TEST_TIME:
                move(BACKWARD)
                log("Moving backward", LOG_CRITICAL)
            elif time.monotonic() - timer[current_state] < 3*TEST_TIME:
                move(HARD_LEFT)
                log("Moving hard left", LOG_CRITICAL)
            elif time.monotonic() - timer[current_state] < 4*TEST_TIME:
                move(HARD_RIGHT)
                log("Moving hard right", LOG_CRITICAL)
            elif time.monotonic() - timer[current_state] < 5*TEST_TIME:
                move(RIGHT)
                log("Turning right", LOG_CRITICAL)
            elif time.monotonic() - timer[current_state] < 6*TEST_TIME:
                move(BACK_RIGHT)
                log("Backing right", LOG_CRITICAL)
            elif time.monotonic() - timer[current_state] < 7*TEST_TIME:
                move(LEFT)
                log("Turning left", LOG_CRITICAL)
            elif time.monotonic() - timer[current_state] < 8*TEST_TIME:
                move(BACK_LEFT)
                log("Backing left", LOG_CRITICAL)
            else:
                move(STOP)


        # Exit
        if not current_state == previous_state:
            log("Leaving state", LOG_INFO)
            pixels.fill(pixels_off)
# /// end of TESTING state ///

    # If we get here, something is wrong, so bail
    else:
        log("I don't know what to do, so heading to IDLE",LOG_CRITICAL)
        current_state = state["IDLE"]


while True:
    conditions = get_conditions()
    # Stop bot with key press
    if not conditions['key_events'] is None and conditions['key_events'].key_number == 1 and conditions['key_events'].pressed:
        current_state = state["IDLE"]
    update_fsm()  # Update the FSM in each iteration
    #time.sleep(0.01)  # Small delay to prevent overwhelming the processor

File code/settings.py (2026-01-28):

# These settings affect the behaviors of your sumobot, such as how fast it moves and
#   how wide of an arc it searches.

MAX_SPEED = 0.8 # Ranges from 0 (doesn't move at all) to 1 (as fast as possible)
MAX_DISTANCE = 600

TURN_DURATION = 0.2 # Number of seconds that the bot spends turning. ***NOT CURRENTLY USED***

CHARGE_DURATION = 5 # Time to charge before giving up
CHARGE_TOLERANCE = 25 # Difference between TOF sensors that triggers a right/left shift

RETREAT_TIME = 1 # Time used in backing up and spinning during a retreat

AVOIDANCE_TIME = 2 # Time to spend during the edge avoidance movement. The slower the motors, the longer this needs to be.

TEST_TIME = 0.5 # Time to spend doing whatever is being done in the test state.

# NONE OF THE VALUES BELOW SHOULD BE CHANGED

WAITING_TIME = 5 # DO NOT CHANGE THIS VALUE! It is the time your bot waits to start battling and must be the same for all bots

LOG_LEVEL = 20 # Sets amount of logging. See below for values, but the way the code is currently written, must use numbers.
# Although not yet tested, setting the LOG_LEVEL to 99 should stop all logging and may speed up bot response
'''
LOG_NOTSET      =  0
LOG_DEBUG       = 10
LOG_INFO        = 20
LOG_WARNING     = 30
LOG_ERROR       = 40
LOG_CRITICAL    = 50
'''

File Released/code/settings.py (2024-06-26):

import board


################################################################
# Settings that control fight mode parameters
# Adjusting these values is an easy way to change your strategy.
################################################################

# Maximum enemy targeting range
MAX_DISTANCE = 600

# Time to charge forward before checking sensors
CHARGE_INTERVAL = 0.05

# Maximum number of seconds to charge before assuming stalemate
MAX_CHARGE_TIME = 5

# Number of seconds to back away from opponent when stalemate detected
BACK_AWAY_TIME = 2

# Maximum charging speed (0-1)
MAX_SPEED = 0.7

# Turning speed (0-1)
TURN_SPEED = 0.5

# Turning duration in seconds when searching for opponent
TURN_DURATION = 0.5


##################################################
# Robot hardware settings
# Change these if your robot is wired differently
# than the instructions, you renegade.
##################################################

# Pin connected to piezo buzzer
PIEZO_PIN = board.GP22

# Pins connected to DC motors (swap variable names if your motors are connected differently)
RIGHT_MOTOR_PIN_B = board.GP11
RIGHT_MOTOR_PIN_A = board.GP10
LEFT_MOTOR_PIN_A = board.GP8
LEFT_MOTOR_PIN_B = board.GP9

# Pin connected to NeoPixels
NEO_PIXEL_PIN = board.GP18

# Pins connected to buttons
BUTTON_1_PIN = board.GP20
BUTTON_2_PIN = board.GP21

# Pins connected to TOF sensors
LEFT_EDGE_SENSOR_PIN = board.GP5
RIGHT_EDGE_SENSOR_PIN = board.GP26
TOF_LEFT_I2C_PINS = (board.GP17, board.GP16)
TOF_RIGHT_I2C_PINS = (board.GP3, board.GP2)
I2C_LEFT_TOGGLE_PIN = board.GP4
I2C_RIGHT_TOGGLE_PIN = board.GP6

# Pin for battery voltage reference path
BATTERY_VOLTAGE_PIN = board.A3
# Low battery threshold voltage
BATTERY_VOLTAGE_THRESHOLD = 52500

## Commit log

2024-08-25 Update assembly instructions.pdf
2026-01-28 chore: reorganize directories for new design
    [1x4 AA battery holder.stl, 2x2 AA battery holder.stl, K345-wheel-42x19mm lowres.stl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]
2026-01-28 chore: update folder structure with gen 2 code and models
    [ks4 blade1.stl, ks4 chassis.stl, ks4 mount.stl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]
